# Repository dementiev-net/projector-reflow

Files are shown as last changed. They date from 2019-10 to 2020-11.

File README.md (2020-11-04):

Пайка SMD на прожекторе по профилю
========================

Контроллер галогенового прожектора для пайки паяльной пастой SMD по профилю. Благодаря термопрофилю получаем качественно запаянные компоненты без следов флюса.

Суть заключается в том, что весь процесс пайки разбит на несколько режимов нагрева.
Сначала идет предварительный нагрев, он позволяет снизить тепловой удар на электронные компоненты.
Далее стадия активации флюса, тек же в ней происходит температурное выравнивание всех компонентов.
Далее стадия оплавления пасты, здесь температура повышается до плавления припоя в пасте и происходит сама пайка.
И наконец стадия охлаждения.
Благодаря термопрофилю получаем качественно запаянные компоненты без следов флюса.

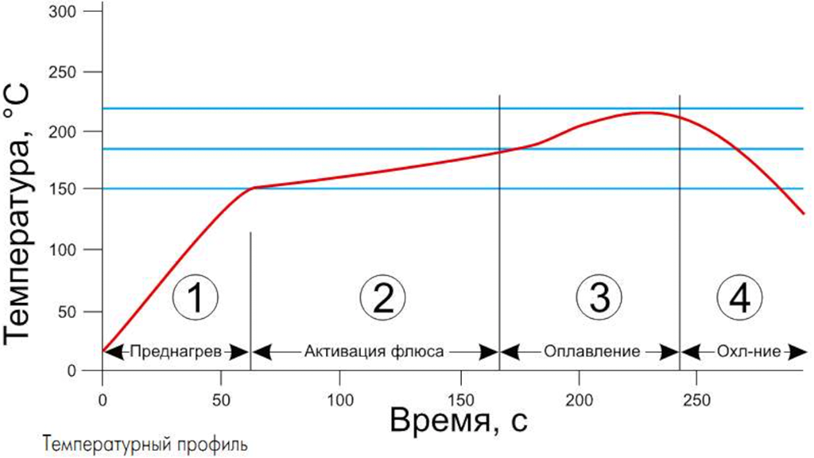
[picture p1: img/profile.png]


## Плата

| Верх | Низ
|---|---
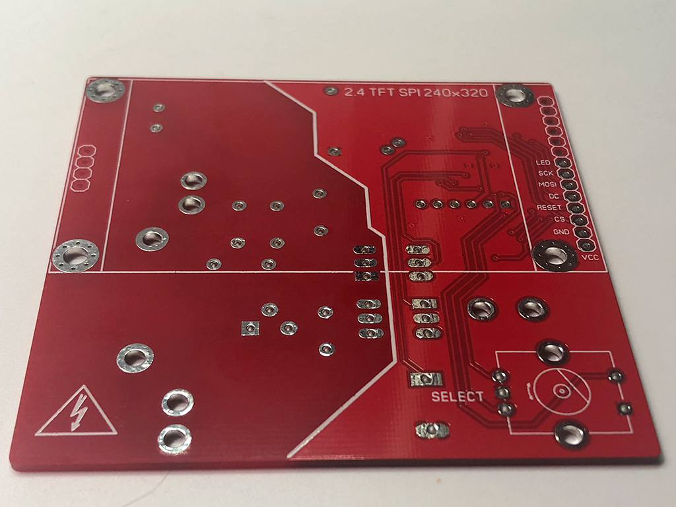
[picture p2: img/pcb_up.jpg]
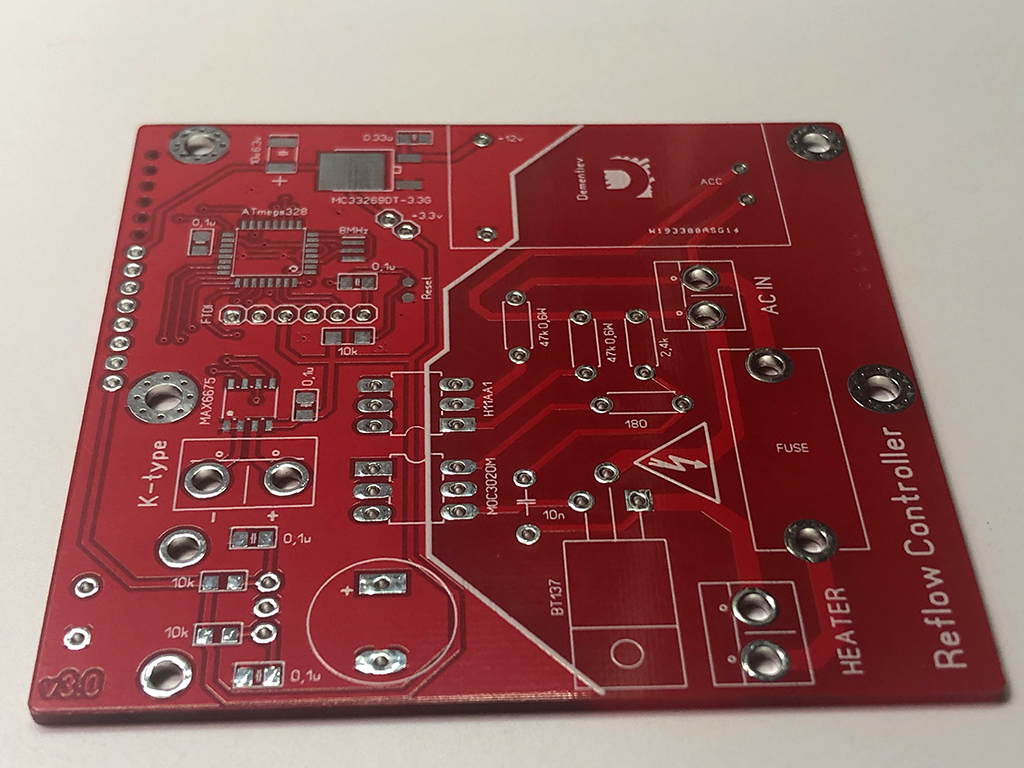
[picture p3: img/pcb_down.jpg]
|   | 

Разделена высоковольтная и низковольтная часть. Убрана заливка платы.
Arduino Nano распаяна прямо на плату. Также распаян датчик температуры. Точнее его микросхема.
Появился трансформатор питающий низковольтную часть. Теперь не нужен блок питания.
Заменен экран 1.8" на 2.4" с более высоким разрешением. У него логическая часть 3.3 вольта, соответственно 
на плате есть стабилизатор питающий экран и Атмегу этим напряжением.
Распаян энкодер.
Остальное как у автора.

| Верх | Низ
|---|---
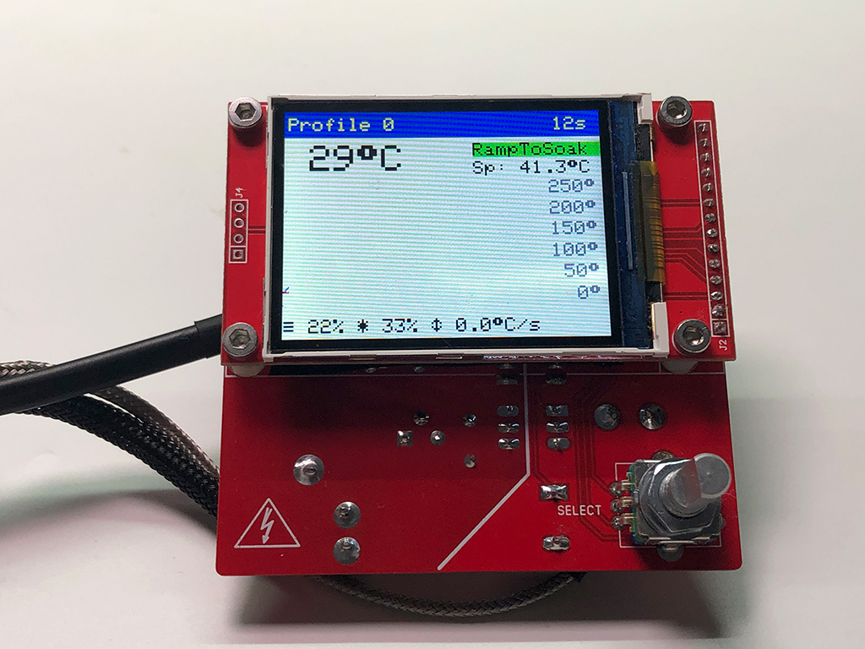
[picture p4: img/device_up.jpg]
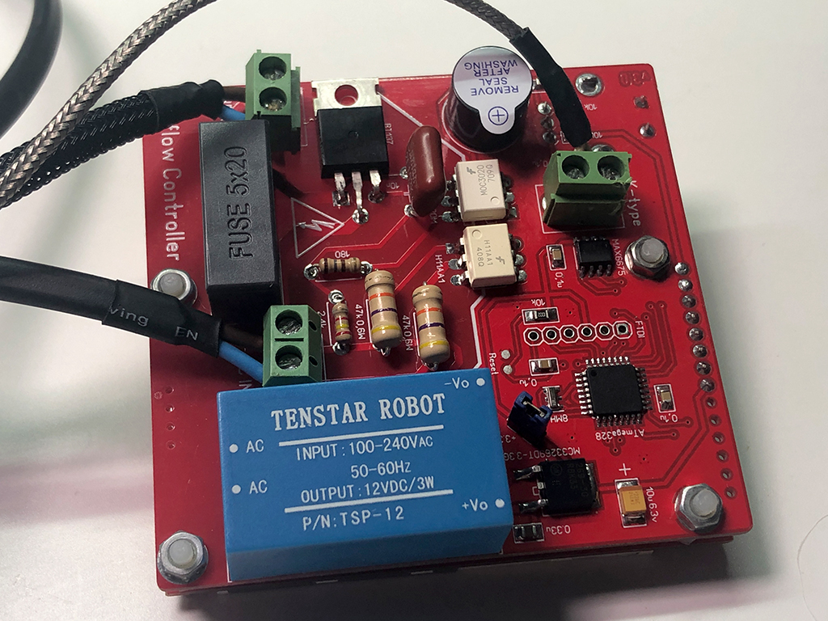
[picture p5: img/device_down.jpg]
|   | 

#### BOM:

|No|Name|Value|Layer|Comment
|---|---|---|---|---
|1|C1|0.33u|Bottom|0805
|2|C2|10u 6.3v|Bottom|Tantal
|3|C3|0.1u|Bottom|0805
|4|C4|0.1u|Bottom|0805
|5|C5|0.1u|Bottom|0805
|6|C6|0.1u|Bottom|0805
|7|C7|0.1u|Bottom|0805
|8|C8|10n|Bottom|К73-17
|9|Q1|8Mhz|Bottom|
|10|Q2|Buzzer|Bottom|
|11|R1|10k|Bottom|0805
|12|R2|10k|Bottom|0805
|13|R3|10k|Bottom|0805
|14|R4|47k|Bottom|0.6W
|15|R5|47k|Bottom|0.6W
|16|R6|2.4k|Bottom|0.25W
|17|R7|180R|Bottom|0.25W
|18|S1|Encoder|Top|
|19|S2|301-021-12|Bottom|
|20|S3|301-021-12|Bottom|
|21|S4|301-021-12|Bottom|
|22|S5|Fuse|Bottom|
|23|SCREEN|2.4 TFT|Top|SPI 240x320
|24|T1|TSP-12|Bottom|220v/12v
|25|U1|Atmega328|Bottom|
|26|U2|MC33269DT-3.3G|Bottom|D-PAK
|27|U3|MAX6675|Bottom|SO-8
|28|U4|H11AA1|Bottom|DIP6
|29|U5|MOC3020M|Bottom|DIP6
|30|U6|BT137|Bottom|TO-220AB

## Корпус

Все построено на обычном 500-ватном галогеновом прожекторе из любого магазина стройматериалов.
Несмотря на его пластиковый корпус температура нагреваемая лампой уходит за 300 градусов, что вполне хватит чтобы расплавить пасту.
Также для равномерности нагревания утеплил его базальтовой ватой и обшил алюминием.
Прибор очень понравился в работе. Но есть и косяк. Лампа всеже не равномерно нагревает пространство.
И прибор подходит для мелких плат которые располагаются по середине прожектора.

| Внутри | Снаружи
|---|---
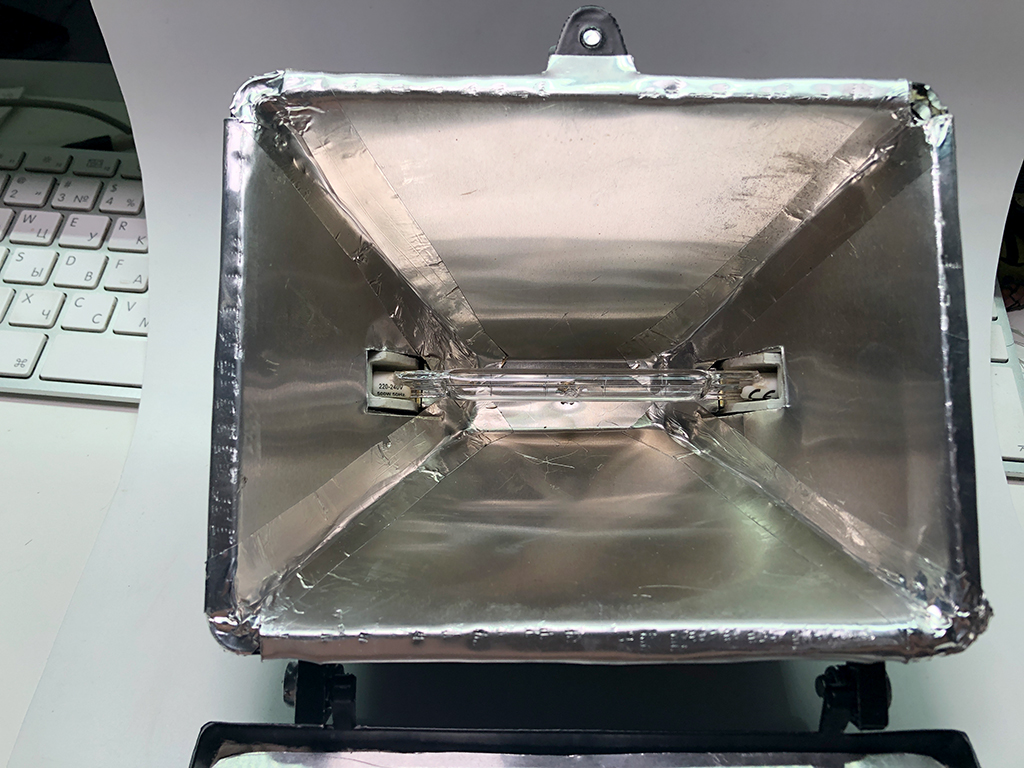
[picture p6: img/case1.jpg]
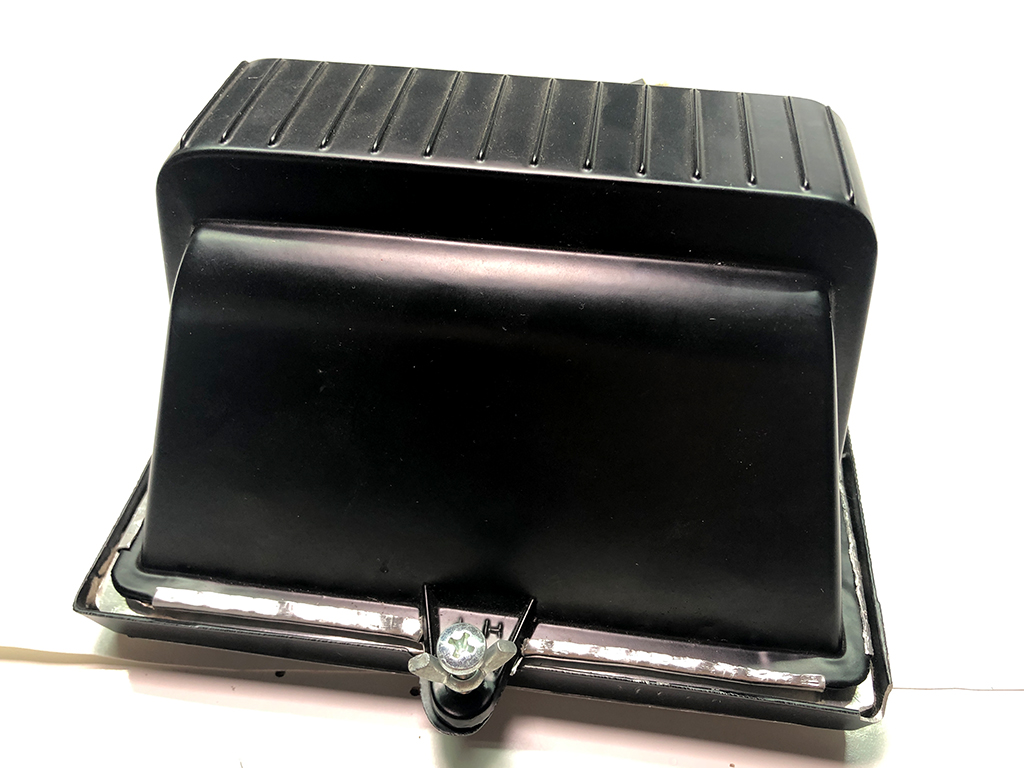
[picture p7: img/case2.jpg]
|   | 
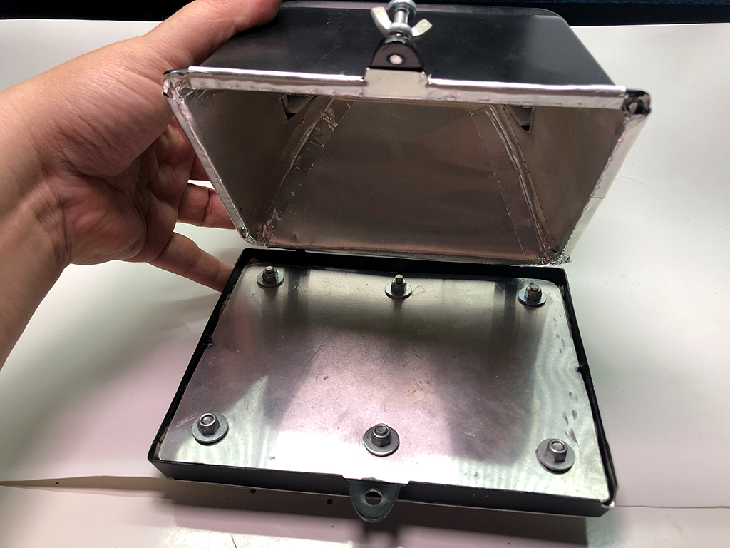
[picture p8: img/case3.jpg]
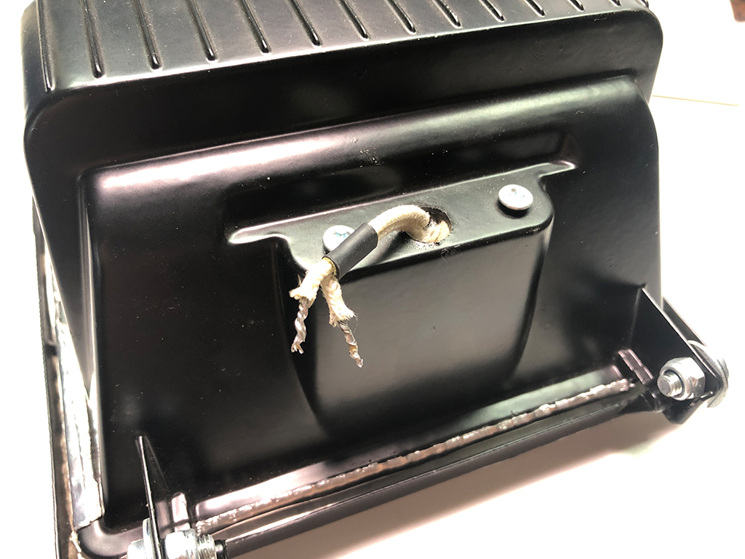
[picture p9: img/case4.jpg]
|   | 

## Прошивка

* Любым программатором загружается bootloader (HEX файл и фьюзы прилагаются). Самой простой вариант прошить через USB Arduino NANO и "сдуть" с нее чип.
* Впаивается чип на плату.
* Заливается INO файл из Arduino IDE (как Arduino NANO) с помощью USB-UART преобразователя (FTDI).

## Контакты

GitHub автора: [https://github.com/dasaki/nanoReflowController](https://github.com/dasaki/nanoReflowController)

Связаться со мной: info@dementiev.net

##### Лицензия: «Attribution-NonCommercial-ShareAlike»<br>(«Атрибуция — Некоммерческое использование — На тех же условиях») 4.0 Всемирная



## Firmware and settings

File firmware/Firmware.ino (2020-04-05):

// ----------------------------------------------------------------------------
// Reflow Oven Controller
// (c) 2019 Дмитрий Дементьев <dementiev@me.com>
// (c) 2017 David Sanz Kirbis
// (c) 2014 Karl Pitrich <karl@pitrich.com>
// (c) 2012-2013 Ed Simmons
// ----------------------------------------------------------------------------

#include "config.h"
#include <avr/eeprom.h>
#include <EEPROM.h>
#include <PID_v1r.h>
#include <SPI.h>
#include <PDQ_GFX.h>
#include "PDQ_ILI9341_config.h"
#include <PDQ_ILI9341.h>
#include <Menu.h>
#include <ClickEncoder.h>
#include <TimerOne.h>
#include "max6675.h"
#include "ports.h"
#include "temperature.h"
#include "helpers.h"
#include "eeprom.h"
#include "ui.h"

volatile uint32_t    timerTicks       = 0;
volatile uint8_t     phaseCounter     = 0;
static const uint8_t TIMER1_PERIOD_US = 200;
uint32_t lastUpdate        = 0;
uint32_t lastDisplayUpdate = 0;
State    previousState     = Idle;
bool     stateChanged      = false;
uint32_t stateChangedTicks = 0;

PID PID(&Input, &Output, &Setpoint, heaterPID.Kp, heaterPID.Ki, heaterPID.Kd, DIRECT);

typedef struct {
  double temp;
  uint16_t ticks;
} Temp_t;

Temp_t airTemp[NUM_TEMP_READINGS];

double readingsT1[NUM_TEMP_READINGS]; // the readings used to make a stable temp rolling average
double runningTotalRampRate;
double rateOfRise = 0;          // the result that is displayed
double totalT1 = 0;             // the running total
double averageT1 = 0;           // the average
uint8_t index = 0;              // the index of the current reading
uint8_t thermocoupleErrorCount;

/**
   Ensure that Solid State Relais are off when starting
*/
void setupPins(void) {

  pinAsOutput(PIN_HEATER);
  digitalLow(PIN_HEATER); // off
  pinAsOutput(PIN_FAN);
  digitalHigh(PIN_FAN);
  pinAsInputPullUp(PIN_ZX);
  pinAsOutput(PIN_TC_CS);
  pinAsOutput(ILI9341_CS_PIN);
  pinAsOutput(PIN_TC_CS);
  pinAsOutput(PIN_BEEPER);
}

/**
   killRelayPins
*/
void killRelayPins(void) {

  Timer1.stop();
  detachInterrupt(INT_ZX);
  digitalHigh(PIN_FAN);
  digitalHigh(PIN_HEATER);
  //PORTD |= (1 << PIN_HEATER) | (1 << PIN_FAN); // off
}

// ----------------------------------------------------------------------------
// wave packet control: only turn the solid state relais on for a percentage
// of complete sinusoids (i.e. 1x 360°)
#define CHANNELS       2
#define CHANNEL_HEATER 0
#define CHANNEL_FAN    1

typedef struct Channel_s {
  volatile uint8_t target; // percentage of on-time
  uint8_t state;           // current state counter
  int32_t next;            // when the next change in output shall occur
  bool action;             // hi/lo active
  uint8_t pin;             // io pin of solid state relais
} Channel_t;

Channel_t Channels[CHANNELS] = {
  // heater
  { 0, 0, 0, false, PIN_HEATER },
  // fan
  { 0, 0, 0, false, PIN_FAN }
};

// delay to align relay activation with the actual zero crossing
uint16_t zxLoopDelay = 0;

// ----------------------------------------------------------------------------
//                             ZERO CROSSING ISR
// ----------------------------------------------------------------------------
/**
   zeroCrossingIsr
   Zero Crossing ISR; per ZX, process one channel per interrupt only
   NB: use native port IO instead of digitalWrite for better performance
*/
void zeroCrossingIsr(void) {

  static uint8_t ch = 0;

  // reset phase control timer
  phaseCounter = 0;
  TCNT1 = 0;
  zeroCrossTicks++;
  // calculate wave packet parameters
  Channels[ch].state += Channels[ch].target;
  if (Channels[ch].state >= 100) {
    Channels[ch].state -= 100;
    Channels[ch].action = false;
  }
  else {
    Channels[ch].action = true;
  }
  Channels[ch].next = timerTicks + zxLoopDelay; // delay added to reach the next zx
  ch = ((ch + 1) % CHANNELS); // next channel
}

/**
   timerIsr
   timer interrupt handling
*/
void timerIsr(void) { // ticks with 100µS

  static uint32_t lastTicks = 0;

  // phase control for the fan
  if (++phaseCounter > 90) {
    phaseCounter = 0;
  }
  if (phaseCounter > Channels[CHANNEL_FAN].target) {
    digitalLow(Channels[CHANNEL_FAN].pin);
  }
  else {
    digitalHigh(Channels[CHANNEL_FAN].pin);
  }
  // wave packet control for heater
  if (Channels[CHANNEL_HEATER].next > lastTicks // FIXME: this looses ticks when overflowing
      && timerTicks > Channels[CHANNEL_HEATER].next)
  {
    if (Channels[CHANNEL_HEATER].action) digitalLow(Channels[CHANNEL_HEATER].pin); //digitalWriteFast(Channels[CHANNEL_HEATER].pin, HIGH);
    else digitalHigh(Channels[CHANNEL_HEATER].pin);//digitalWriteFast(Channels[CHANNEL_HEATER].pin, LOW);
    lastTicks = timerTicks;
  }
  // handle encoder + button
  if (!(timerTicks % 10)) {
    Encoder.service();
  }
  timerTicks++;
}

/**
   abortWithError
*/
void abortWithError(int error) {

  killRelayPins();
  displayError(error);
}

/**
   setup
*/
void setup() {

  setupPins();
  setupTFT();
  if (firstRun()) {
    factoryReset();
    loadParameters(0);
  }
  else {
    loadLastUsedProfile();
  }
  do {
    // wait for MAX chip to stabilize
    delay(500);
    readThermocouple();
  }

  while ((tcStat > 0) && (thermocoupleErrorCount++ < TC_ERROR_TOLERANCE));
  if ((tcStat != 0) || (thermocoupleErrorCount  >= TC_ERROR_TOLERANCE)) {
    abortWithError(tcStat);
  }
  // initialize moving average filter
  runningTotalRampRate = temperature * NUM_TEMP_READINGS;
  for (int i = 0; i < NUM_TEMP_READINGS; i++) {
    airTemp[i].temp = temperature;
  }
  loadFanSpeed();
  loadPID();
  PID.SetOutputLimits(0, 100); // max output 100%
  PID.SetSampleTime(PID_SAMPLE_TIME);
  PID.SetMode(AUTOMATIC);
  delay(1000);
  tone(PIN_BEEPER, BEEP_FREQ, 100);
  displaySplash();
  zxLoopDelay = DEFAULT_LOOP_DELAY;
  menuExit(Menu::actionDisplay); // reset to initial state
  MenuEngine.navigate(&miCycleStart);
  currentState = Settings;
  menuUpdateRequest = true;
  Timer1.initialize(TIMER1_PERIOD_US);
  Timer1.attachInterrupt(timerIsr);
  attachInterrupt(INT_ZX, zeroCrossingIsr, RISING);
  delay(100);
}

uint32_t lastRampTicks;
uint32_t lastSoakTicks;

/**
   updateRampSetpoint
*/
void updateRampSetpoint(bool down = false) {

  if (zeroCrossTicks > lastRampTicks + TICKS_PER_UPDATE) {
    double rate = (down) ? activeProfile.rampDownRate : activeProfile.rampUpRate;
    Setpoint += (rate / (float)TICKS_PER_SEC * (zeroCrossTicks - lastRampTicks)) * ((down) ? -1 : 1);
    lastRampTicks = zeroCrossTicks;
  }
}

/**
   updateSoakSetpoint
*/
void updateSoakSetpoint(bool down = false) {

  if (zeroCrossTicks > lastSoakTicks + TICKS_PER_UPDATE) {
    double rate = (activeProfile.soakTempB - activeProfile.soakTempA) / (float)activeProfile.soakDuration;
    Setpoint += (rate / (float)TICKS_PER_SEC * (zeroCrossTicks - lastSoakTicks)) * ((down) ? -1 : 1);
    lastSoakTicks = zeroCrossTicks;
  }
}

/**
   loop
*/
void loop(void) {

  // handle encoder
  encMovement = Encoder.getValue();
  if (encMovement) {
    encAbsolute += encMovement;
    if (currentState == Settings) {
      MenuEngine.navigate((encMovement > 0) ? MenuEngine.getNext() : MenuEngine.getPrev());
      menuUpdateRequest = true;
    }
  }
  // handle button
  switch (Encoder.getButton()) {
    case ClickEncoder::Clicked:
      if (currentState == Complete) { // at end of cycle; reset at click
        menuExit(Menu::actionDisplay); // reset to initial state
        MenuEngine.navigate(&miCycleStart);
        currentState = Settings;
        menuUpdateRequest = true;
      }
      else if (currentState < UIMenuEnd) {
        menuUpdateRequest = true;
        MenuEngine.invoke();
      }
      else if (currentState > UIMenuEnd) {
        currentState = CoolDown;
      }
      break;
    case ClickEncoder::DoubleClicked:
      if (currentState < UIMenuEnd) {
        if (MenuEngine.getParent() != &miExit) {
          MenuEngine.navigate(MenuEngine.getParent());
          menuUpdateRequest = true;
        }
      }
      break;
  }
  // update current menu item while in edit mode
  if (currentState == Edit) {
    if (MenuEngine.currentItem != &Menu::NullItem) {
      MenuEngine.executeCallbackAction(Menu::actionDisplay);
    }
  }
  // handle menu update
  if (menuUpdateRequest) {
    menuUpdateRequest = false;
    if (currentState < UIMenuEnd && !encMovement && currentState != Edit && previousState != Edit) { // clear menu on child/parent navigation
      tft.fillScreen(ILI9341_WHITE);
    }
    MenuEngine.render(renderMenuItem, menuItemsVisible);
  }
  // track state changes
  if (currentState != previousState) {
    stateChangedTicks = zeroCrossTicks;
    stateChanged = true;
    previousState = currentState;
  }
  if (zeroCrossTicks - lastUpdate >= TICKS_PER_UPDATE) {
    uint32_t deltaT = zeroCrossTicks - lastUpdate;
    lastUpdate = zeroCrossTicks;
    readThermocouple(); // should be sufficient to read it every 250ms or 500ms
    if (tcStat > 0) {
      thermocoupleErrorCount++;
      if ((thermocoupleErrorCount > TC_ERROR_TOLERANCE) && (currentState != Edit)) {
        abortWithError(tcStat);
      } else thermocoupleErrorCount = 0;
    } else {
      thermocoupleErrorCount = 0;
      // rolling average of the temp T1 and T2
      totalT1 -= readingsT1[index];       // subtract the last reading
      readingsT1[index] = temperature;
      totalT1 += readingsT1[index];       // add the reading to the total
      index = (index + 1) % NUM_TEMP_READINGS;  // next position
      averageT1 = totalT1 / (float)NUM_TEMP_READINGS;  // calculate the average temp
      // need to keep track of a few past readings in order to work out rate of rise
      for (int i = 1; i < NUM_TEMP_READINGS; i++) { // iterate over all previous entries, moving them backwards one index
        airTemp[i - 1].temp = airTemp[i].temp;
        airTemp[i - 1].ticks = airTemp[i].ticks;
      }
      airTemp[NUM_TEMP_READINGS - 1].temp = averageT1; // update the last index with the newest average
      airTemp[NUM_TEMP_READINGS - 1].ticks = (uint16_t)deltaT;
      // calculate rate of temperature change
      uint32_t collectTicks = 0;
      for (int i = 0; i < NUM_TEMP_READINGS; i++) {
        collectTicks += airTemp[i].ticks;
      }
      float tempDiff = (airTemp[NUM_TEMP_READINGS - 1].temp - airTemp[0].temp);
      float timeDiff = collectTicks / (float)(TICKS_PER_SEC);
      rampRate = tempDiff / timeDiff;
      Input = airTemp[NUM_TEMP_READINGS - 1].temp; // update the variable the PID reads
    }
    // display update
    if (zeroCrossTicks - lastDisplayUpdate >= TICKS_TO_REDRAW) {
      lastDisplayUpdate = zeroCrossTicks;
      if (currentState > UIMenuEnd) {
        updateProcessDisplay();
      }
    }
    switch (currentState) {
      case RampToSoak:
        if (stateChanged) {
          lastRampTicks = zeroCrossTicks;
          stateChanged = false;
          Output = 50;
          PID.SetMode(AUTOMATIC);
          PID.SetControllerDirection(DIRECT);
          PID.SetTunings(heaterPID.Kp, heaterPID.Ki, heaterPID.Kd);
          Setpoint = Input;
          tone(PIN_BEEPER, BEEP_FREQ, 100);
        }
        updateRampSetpoint();
        if (Setpoint >= activeProfile.soakTempA - 1) {
          currentState = Soak;
        }
        break;
      case Soak:
        if (stateChanged) {
          lastSoakTicks = zeroCrossTicks;
          stateChanged = false;
          Setpoint = activeProfile.soakTempA;
        }
        updateSoakSetpoint();
        if (zeroCrossTicks - stateChangedTicks >= (uint32_t)activeProfile.soakDuration * TICKS_PER_SEC) {
          currentState = RampUp;
        }
        break;
      case RampUp:
        if (stateChanged) {
          stateChanged = false;
          lastRampTicks = zeroCrossTicks;
        }
        updateRampSetpoint();
        if (Setpoint >= activeProfile.peakTemp - 1) {
          Setpoint = activeProfile.peakTemp;
          currentState = Peak;
        }
        break;
      case Peak:
        if (stateChanged) {
          stateChanged = false;
          Setpoint = activeProfile.peakTemp;
        }
        if (zeroCrossTicks - stateChangedTicks >= (uint32_t)activeProfile.peakDuration * TICKS_PER_SEC) {
          currentState = RampDown;
        }
        break;
      case RampDown:
        if (stateChanged) {
          stateChanged = false;
          lastRampTicks = zeroCrossTicks;
          PID.SetControllerDirection(REVERSE);
          PID.SetTunings(fanPID.Kp, fanPID.Ki, fanPID.Kd);
          Setpoint = activeProfile.peakTemp - 15; // get it all going with a bit of a kick! v sluggish here otherwise, too hot too long
          tone(PIN_BEEPER, BEEP_FREQ, 3000); // Beep as a reminder that CoolDown starts (and maybe open up the oven door for fast enough cooldown)
        }
        updateRampSetpoint(true);
        if (Setpoint <= idleTemp) {
          currentState = CoolDown;
        }
        break;
      case CoolDown:
        if (stateChanged) {
          stateChanged = false;
          PID.SetControllerDirection(REVERSE);
          PID.SetTunings(fanPID.Kp, fanPID.Ki, fanPID.Kd);
          Setpoint = idleTemp;
        }
        if (Input < (idleTemp + 5)) {
          currentState = Complete;
          PID.SetMode(MANUAL);
          Output = 0;
          tone(PIN_BEEPER, BEEP_FREQ, 500); //End Beep
          delay(1500);
          tone(PIN_BEEPER, BEEP_FREQ, 500);
          delay(1500);
          tone(PIN_BEEPER, BEEP_FREQ, 1500);
        }
    }
  }

  // safety check that we're not doing something stupid.
  // if the thermocouple is wired backwards, temp goes DOWN when it increases
  // during cooling, the t962a lags a long way behind, hence the hugely lenient cooling allowance.
  // both of these errors are blocking and do not exit!
  //if (Setpoint > Input + 50) abortWithError(10); // if we're 50 degree cooler than setpoint, abort
  //if (Input > Setpoint + 50) abortWithError(20); // or 50 degrees hotter, also abort
  PID.Compute();
  // decides which control signal is fed to the output for this cycle
  if (   currentState != RampDown
         && currentState != CoolDown
         && currentState != Settings
         && currentState != Complete
         && currentState != Idle
         && currentState != Settings
         && currentState != Edit)
  {
    heaterValue = Output;
    fanValue = fanAssistSpeed;
  }
  else {
    heaterValue = 0;
    fanValue = Output;
  }
  Channels[CHANNEL_HEATER].target = heaterValue;
  double fanTmp = 90.0 / 100.0 * fanValue; // 0-100% -> 0-90° phase control
  Channels[CHANNEL_FAN].target = 90 - (uint8_t)fanTmp;
}

/**
   saveProfile
*/
void saveProfile(unsigned int targetProfile, bool quiet) {

  activeProfileId = targetProfile;
  if (!quiet) {
    memoryFeedbackScreen(activeProfileId, false);
  }
  saveParameters(activeProfileId); // activeProfileId is modified by the menu code directly, this method is called by a menu action
  if (!quiet) delay(500);
}

/**
   firstRun
*/
bool firstRun() {
  // if all bytes of a profile in the middle of the eeprom space are 255, we assume it's a first run
  unsigned int offset = 15 * sizeof(Profile_t);
  for (uint16_t i = offset; i < offset + sizeof(Profile_t); i++) {
    if (EEPROM.read(i) != 255) {
      return false;
    }
  }
  return true;
}

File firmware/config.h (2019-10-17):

#ifndef CONFIG_H
#define CONFIG_H

const char * ver = "3.0";

// hardware
static const uint8_t PIN_TC_CS  = A0;
static const uint8_t PIN_TC_DO  = A1;
static const uint8_t PIN_TC_CLK = A2;
static const uint8_t PIN_HEATER = 3;
static const uint8_t PIN_FAN    = 1;
static const uint8_t PIN_BEEPER = 10;
static const uint16_t BEEP_FREQ = 1976;  // B6 note
static const uint8_t PIN_ZX = 2; // pin for zero crossing detector
static const uint8_t INT_ZX = digitalPinToInterrupt(PIN_ZX); // interrupt for zero crossing detector
static const uint8_t DEFAULT_LOOP_DELAY = 89;  // should be about 16% less for 60Hz mains
static const uint8_t TICKS_PER_SEC      = 100; // for 50Hz mains:  2*50Hz = 100 ticks per second
static const uint8_t TICKS_PER_UPDATE   = 25;
static const uint8_t TICKS_TO_REDRAW    = 50;

// encoder
static const uint8_t PIN_ENC_A   = A3;
static const uint8_t PIN_ENC_B   = A4;
static const uint8_t PIN_ENC_BTN = A5;
static const uint8_t ENC_STEPS_PER_NOTCH = 4;
static const boolean IS_ENC_ACTIVE = false; // encoder module actively fed with VCC ( seems to works bad if set to true )

// temperature
static const uint8_t NUM_TEMP_READINGS  = 5;
static const uint8_t TC_ERROR_TOLERANCE = 5;    // allow for n consecutive errors due to noisy power supply before bailing out
static const float   TEMP_COMPENSATION  = 1.06; // correction factor to match temperature measured with other device

// profiles
static const uint8_t DEFAULT_SOAK_TEPM_A      = 150;
static const uint8_t DEFAULT_SOAK_TEPM_B      = 180;
static const uint8_t DEFAULT_SOAK_DURATION    = 180;
static const uint8_t DEFAULT_PEAK_TEPM        = 250;
static const uint8_t DEFAULT_PEAK_DURATION    = 60;
static const float DEFAULT_RAMP_UP_RATE       = 1.2; // degrees / second (keep it about 1/2 of maximum to prevent PID overshooting)
static const float DEFAULT_RAMP_DOWN_RATE     = 2.0; // degrees / second
static const uint8_t FACTORY_FAN_ASSIST_SPEED = 33;

// PID
// Kp: Determines how aggressively the PID reacts to the current amount of error (Proportional) (double >=0)
// Ki: Determines how aggressively the PID reacts to error over time (Integral) (double>=0)
// Kd: Determines how aggressively the PID reacts to the change in error (Derivative) (double>=0)
//
// Experimental method to tune PID:
//
// > Set all gains to 0.
// > Increase Kd until the system oscillates.
// > Reduce Kd by a factor of 2-4.
// > Set Kp to about 1% of Kd.
// > Increase Kp until oscillations start.
// > Decrease Kp by a factor of 2-4.
// > Set Ki to about 1% of Kp.
// > Increase Ki until oscillations start.
// > Decrease Ki by a factor of 2-4.
#define PID_SAMPLE_TIME 200
#define FACTORY_KP  1.75
#define FACTORY_KI 0.03
#define FACTORY_KD 3.0

double temperature;
uint8_t tcStat = 0;
double Setpoint;
double Input;
double Output;
uint8_t fanValue;
uint8_t heaterValue;
double rampRate = 0;
typedef struct {
  double Kp;
  double Ki;
  double Kd;
} PID_t;
PID_t heaterPID = { FACTORY_KP, FACTORY_KI,  FACTORY_KD };
PID_t fanPID    = { 1.00, 0.00, 0.00 };
int idleTemp    = 50;                  // the temperature at which to consider the oven safe to leave to cool naturally
uint32_t startCycleZeroCrossTicks;
volatile uint32_t zeroCrossTicks = 0;
char buf[20];
int fanAssistSpeed = 33;               // default fan speed

// state machine
typedef enum {
  None     = 0,
  Idle     = 1,
  Settings = 2,
  Edit     = 3,
  UIMenuEnd = 9,
  RampToSoak = 10,
  Soak,
  RampUp,
  Peak,
  RampDown,
  CoolDown,
  Complete = 20,
  Tune = 30
} State;

State currentState  = Idle;

// data type for the values used in the reflow profile
typedef struct profileValues_s {
  int16_t soakTempA;
  int16_t soakTempB;
  int16_t soakDuration;
  int16_t peakTemp;
  int16_t peakDuration;
  double  rampUpRate;
  double  rampDownRate;
  uint8_t checksum;
} Profile_t;

Profile_t activeProfile; // the one and only instance
int activeProfileId = 0;

const uint8_t maxProfiles = 30;

/**
   makeDefaultProfile
*/
void makeDefaultProfile() {
  activeProfile.soakTempA    = DEFAULT_SOAK_TEPM_A;
  activeProfile.soakTempB    = DEFAULT_SOAK_TEPM_B;
  activeProfile.soakDuration = DEFAULT_SOAK_DURATION;
  activeProfile.peakTemp     = DEFAULT_PEAK_TEPM;
  activeProfile.peakDuration =  DEFAULT_PEAK_DURATION;
  activeProfile.rampUpRate   =   DEFAULT_RAMP_UP_RATE;
  activeProfile.rampDownRate =   DEFAULT_RAMP_DOWN_RATE;
}

#endif // CONFIG_H

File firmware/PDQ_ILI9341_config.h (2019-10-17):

/**
   PDQ_ILI9341 configuration
*/
#define	ILI9341_CS_PIN		6			// <= /CS pin (chip-select, LOW to get attention of ILI9341, HIGH and it ignores SPI bus)
#define	ILI9341_DC_PIN		7			// <= DC pin (1=data or 0=command indicator line) also called RS
#define	ILI9341_RST_PIN		8			// <= RST pin (optional)

// other PDQ library options
#define	ILI9341_SAVE_SPCR	0			// <= 0/1 with 1 to save/restore AVR SPI control register (to "play nice" when other SPI use)

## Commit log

2019-10-17 Добавлено описание
2019-10-17 Правка описания
2019-10-17 Добпален Optiboot и фьюзы
2019-10-17 Добавлен исходник Arduino
2019-10-17 Добавлены Gerber файлы платы
    [Projector Oven-[3.0].DRL, Projector Oven-[3.0]_copper_bottom.gbr, Projector Oven-[3.0]_copper_top.gbr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]
2019-10-17 Обновил описание
2019-10-17 Изменен Optiboot и фьюзы
2019-10-17 Добавлен Optiboot и фьюзы
2019-10-18 Небольшие правки
    [Projector Oven-[3.0].DRL, Projector Oven-[3.0]_copper_bottom.gbr, Projector Oven-[3.0]_copper_top.gbr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]
2019-10-22 Правки описания
2020-04-05 Update Firmware.ino
    Актуальная почта в контактах
2020-06-13 Правка README.md
2020-06-16 Некоммерческая лицензия
2020-11-04 Поменял описание
2020-11-17 Повторная выгрузка на Github
    [Projector Oven-[3.0].DRL, Projector Oven-[3.0]_copper_bottom.gbr, Projector Oven-[3.0]_copper_top.gbr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]
